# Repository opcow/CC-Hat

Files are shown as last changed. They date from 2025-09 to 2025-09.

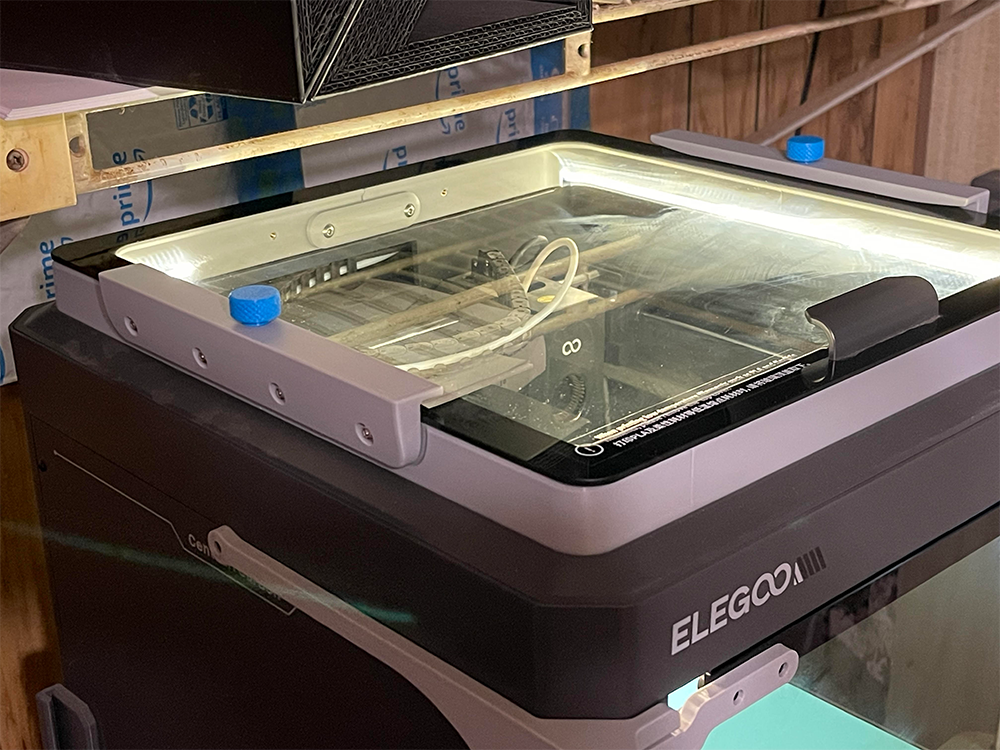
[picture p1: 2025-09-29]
images/main.png

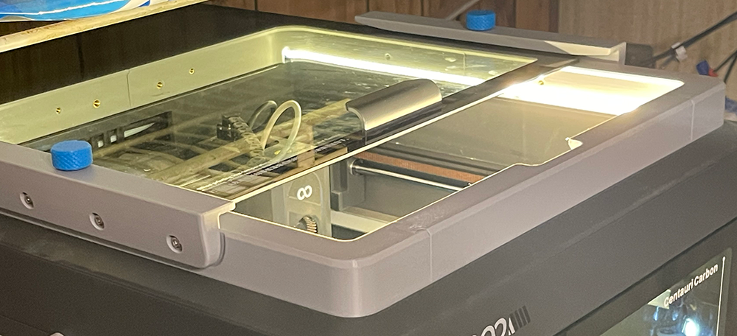
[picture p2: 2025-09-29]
images/open.png

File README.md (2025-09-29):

# CC-Hat (yet another riser)

This is my take on a lid riser for the Centauri Carbon.

I started this design using the one-piece step file for the vented riser by JesusFreak, and while there isn't very much left of the original geometry of that riser, I'm calling this a remix of JesusFreak's awesome design.

### Changes From the OG

* Reduced height to 27.5 MM.
* No vent. The riser is designed so that the lid can be slid back or forward for venting.

### Important Things to Know Before Printing

* All holes were sized for M3 and M4 threaded inserts. I have provided step files, so the holes can be resized if you prefer not to use threaded inserts (though I recommend using them for the 8 M4 screws for the glass guides).
* All holes other than the 8 glass guide holes are completely optional. Other than the guides, the parts fit together with dovetail joints which should be entirely sufficient to hold the riser together while in place on the printer.
* The dovetail joints were designed with **zero tolerance**. This makes for a perfect tight, but not too tight, fit when I print them on my printer using my slicer settings. I would strongly suggest that you print the provided test joint to ensure that these joints will work for you before printing the whole shebang. Adjust the tolerance if needed.
* The parts called plates are provided for locking the joints. These are optional. The holes are sized for M3 inserts. Resize the holes if you want to self tap screws into the plastic.
* **The thumbscrews are intended to be printed in 95A TPU**. TPU gives good friction and it would be impossible to break the glass by over-tightening the screw.
* The inside holes are meant for hooks/clamps for holding an LED strip. I use a strip with an adhesive backing and don't use these holes for anything, there are example clamp models provided.

### Other Info

The guides should allow the glass to be lifted enough for the handle screws to clear the riser frame for inserting the glass or the glass can be inserted from the rear. There is a spacer meant to go between the guide and the frame. This allows for tighter or looser horizontal tolerance between the glass and the guides. The provided spacer model is 2.1 MM thick. You will need to print 8 of these.

There is an optional glass guide without the threaded hole if you only want to use a single thumbscrew or no thumbscrews. I like using two thumbscrews, as it makes it easy to safely remove the whole riser with the glass in place (just make sure the screws are locked down first).

There is an optional rear brace provided for the inside rear dovetail joint. This part is optional, and really is overkill if you are using the rear plate part, but it's there if you want.

### Print Materials and Settings

Use whatever you want for the frame and guides. PLA or PETG should be fine.

As stated above, I recommend 95A TPU for the thumbscrews. I haven't tried other materials. The purpose of the screws is to hold the glass in place when closed or when open for venting. You could adjust the spacers to achieve enough friction between the glass and the guides to keep the glass in place. I have not tested this.

The front part of the frame must be printed at 45 degrees on a 256 x 256 build plate. I change the sparse infill direction to 0 and the solid infill to 90 to compensate.

I used Orca Slicer's 0.20 MM Strength preset with gyroid for the frame, which I printed in Voxel PLA.

I used the 0.16 MM Optimal preset with gyroid infill for the guides, which were also printed in Voxel PLA.

I used the 0.16 MM Optimal preset with gyroid infill for the thumbscrews, which were printed in Polymaker 95A TPU.

I use scarf joint seam, nearest for my seam settings and I can't even tell where the seams are, but use whatever you prefer.

### Required Extras

* 8 M4 x 12 MM button head screws. Socket cap may be okay, as well, but you might want to use a washer.
* 8 M4 threaded inserts (or resize the holes for self-tapping).
* Optionally, 7 M3 x 8 MM counter-sink socket head screws and M3 inserts (or resize the holes for self-tapping).
* 2 M4 screws and inserts if you want the rear joint brace, but this part isn't really recommended if you are using the three plates that go under the joints.

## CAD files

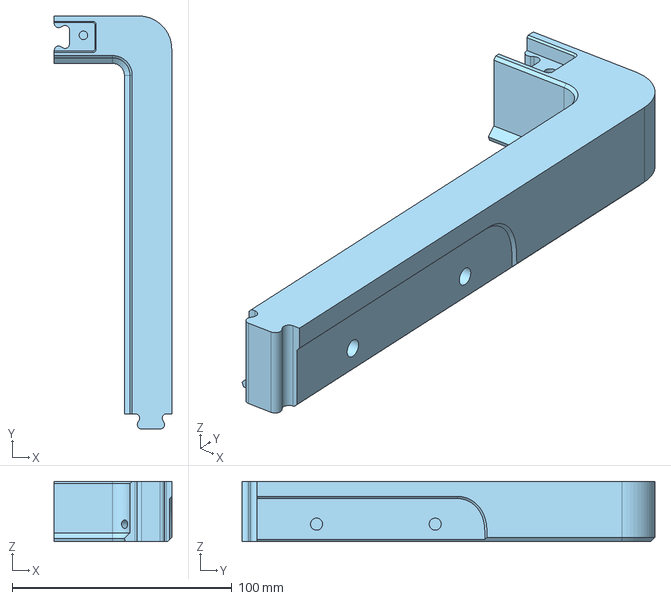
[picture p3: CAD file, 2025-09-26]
STEP/front-right.step
53.5 x 187.9 x 27.5 mm

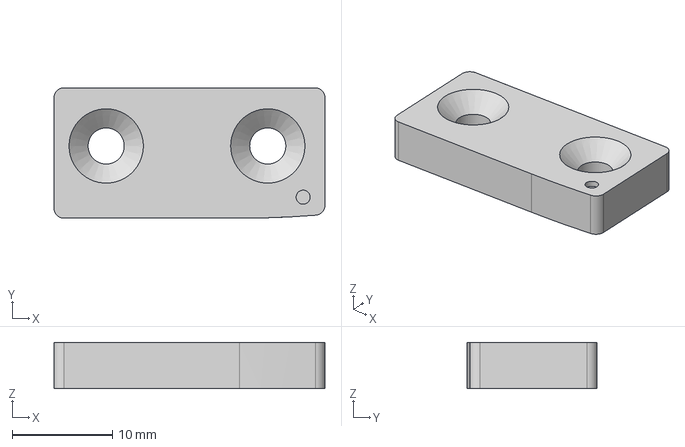
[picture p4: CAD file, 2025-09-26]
STEP/plate-left.step
27.0 x 13.0 x 4.60 mm

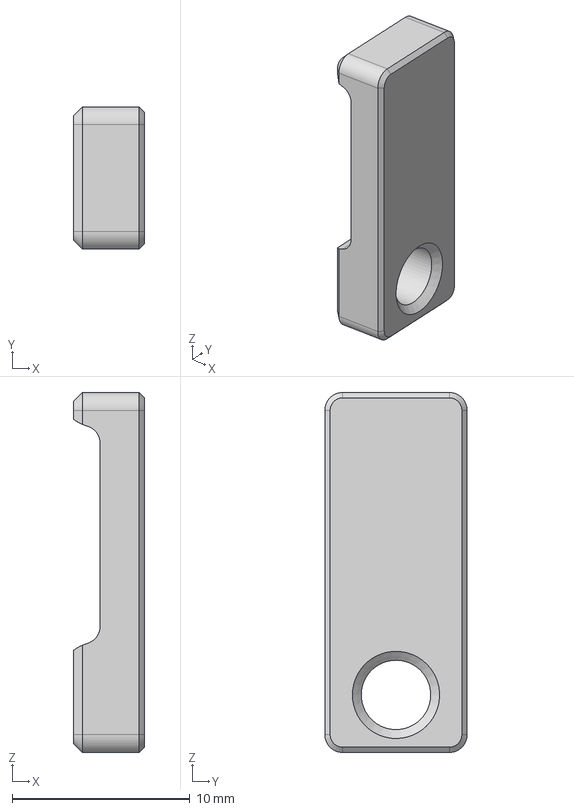
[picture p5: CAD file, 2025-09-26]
STEP/clamp.step
4.00 x 8.00 x 20.2 mm

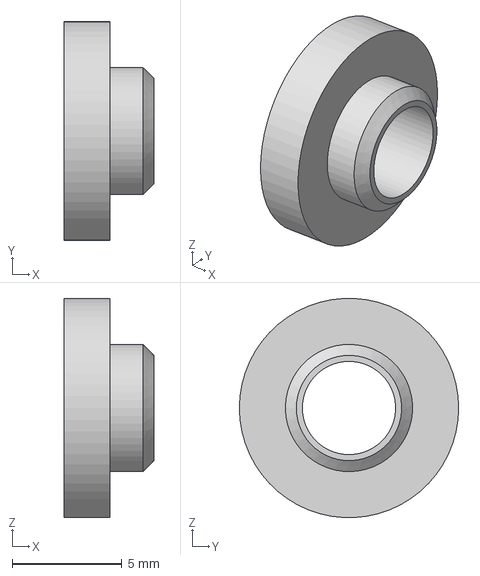
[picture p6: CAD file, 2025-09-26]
STEP/spacer.step
4.10 x 10.0 x 9.99 mm

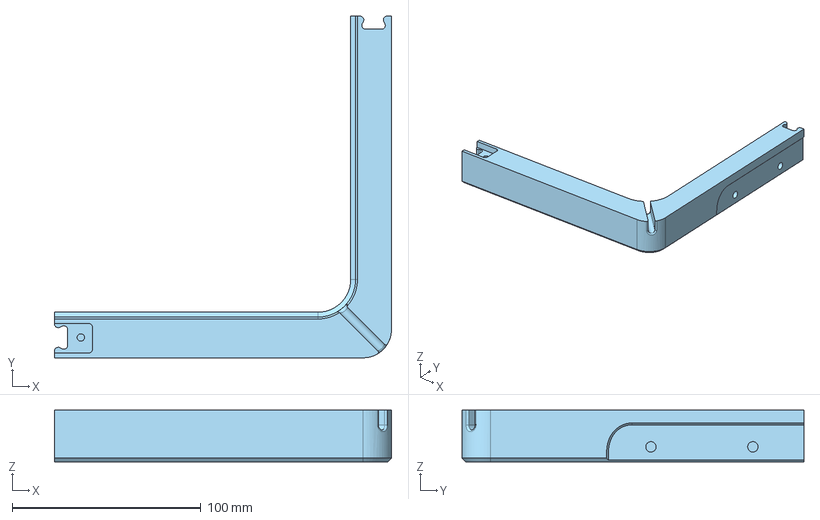
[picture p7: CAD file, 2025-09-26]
STEP/back-right.step
178.5 x 181.0 x 27.5 mm

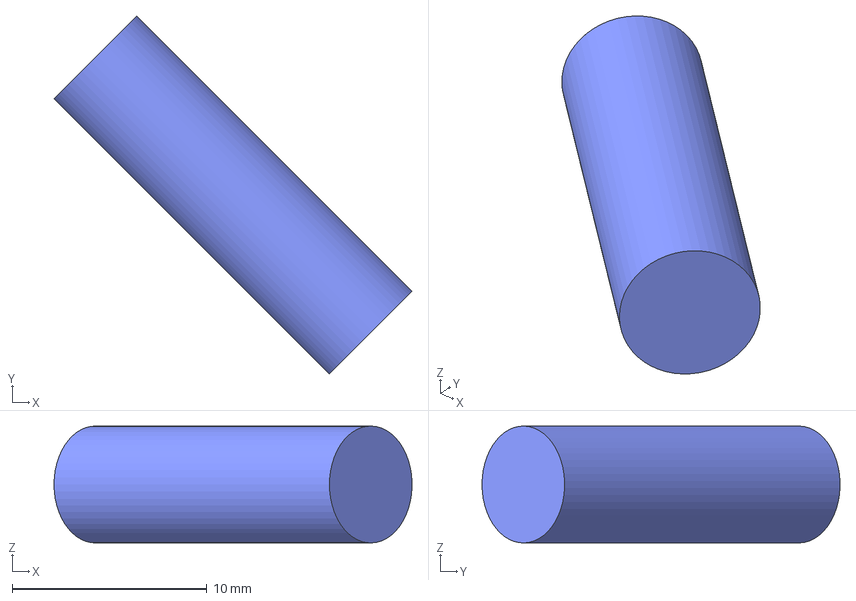
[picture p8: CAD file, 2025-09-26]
STEP/plug.step
18.4 x 18.4 x 6.00 mm

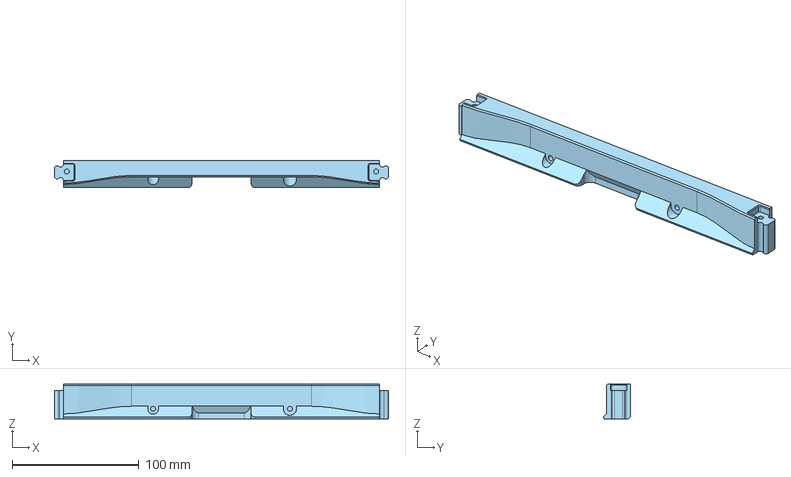
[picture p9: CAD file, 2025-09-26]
STEP/front.step
263.9 x 21.6 x 27.5 mm

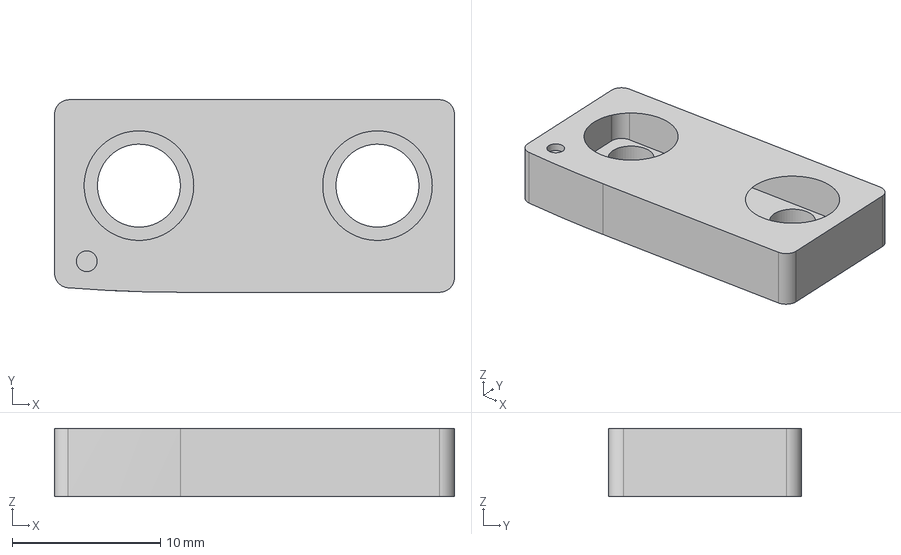
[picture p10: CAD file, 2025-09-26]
STEP/plate-right.step
27.0 x 13.0 x 4.60 mm

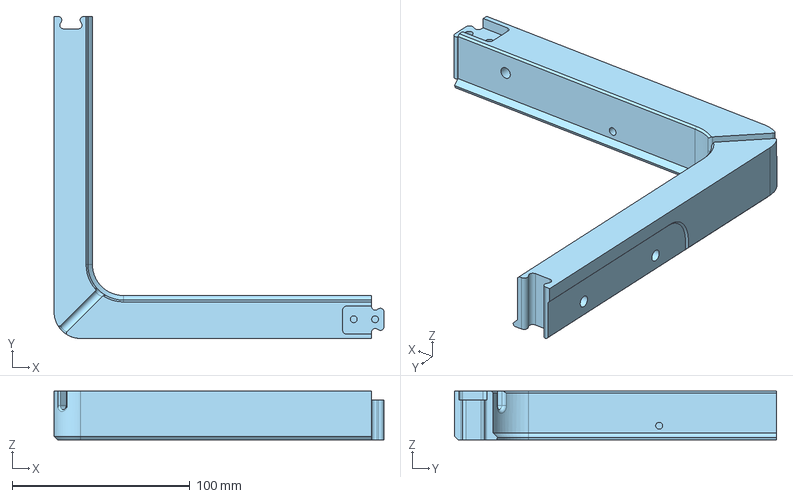
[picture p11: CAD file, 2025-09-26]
STEP/back-left.step
185.4 x 181.0 x 27.5 mm

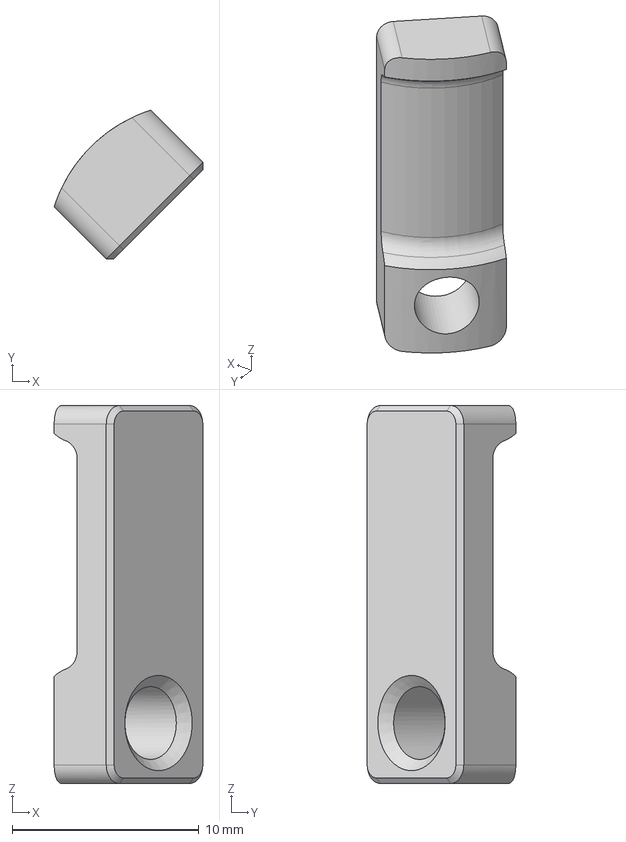
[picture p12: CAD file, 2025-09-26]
STEP/corner-clamp.step
7.96 x 7.96 x 20.2 mm

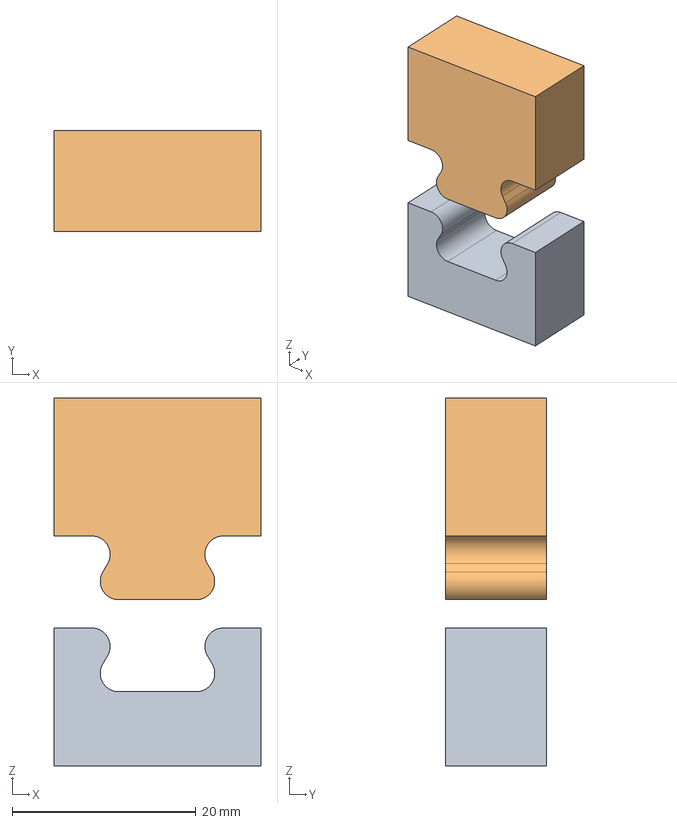
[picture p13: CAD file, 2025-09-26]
STEP/test-joint.step
22.5 x 11.0 x 40.0 mm

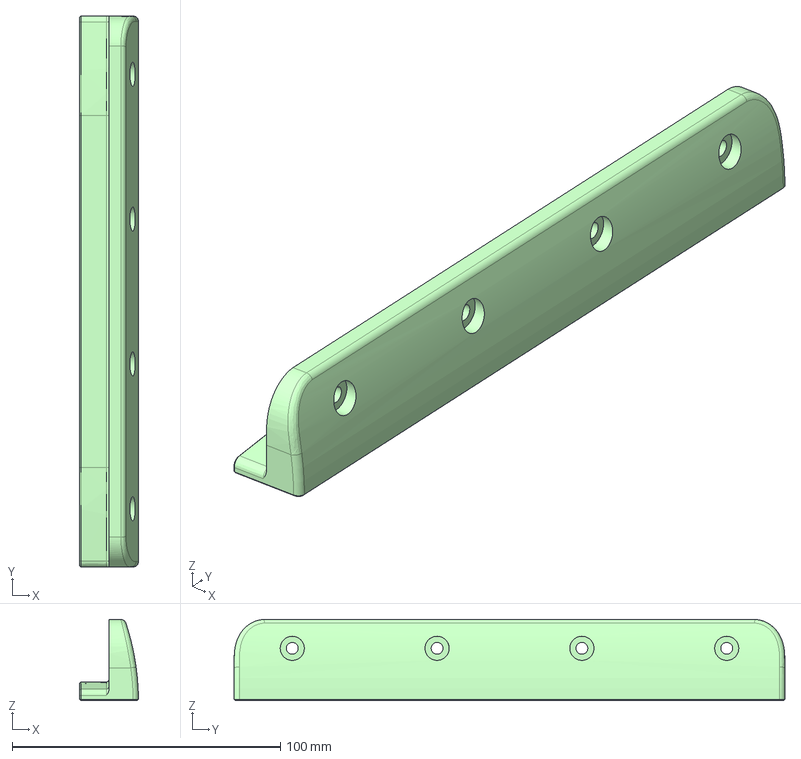
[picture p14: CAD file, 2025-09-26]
STEP/guide.step
22.0 x 205.5 x 30.3 mm

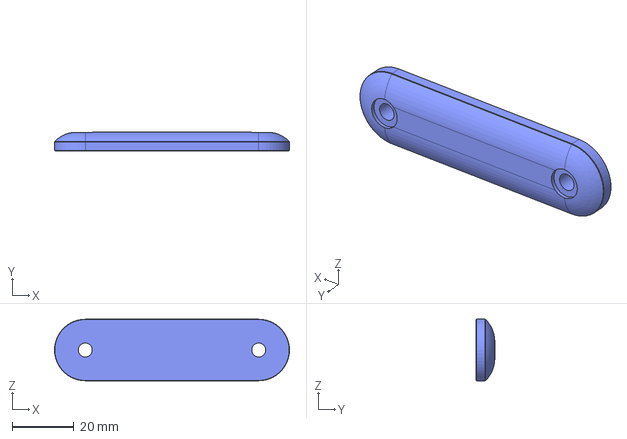
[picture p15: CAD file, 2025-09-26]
STEP/rear-brace.step
76.0 x 6.00 x 19.9 mm

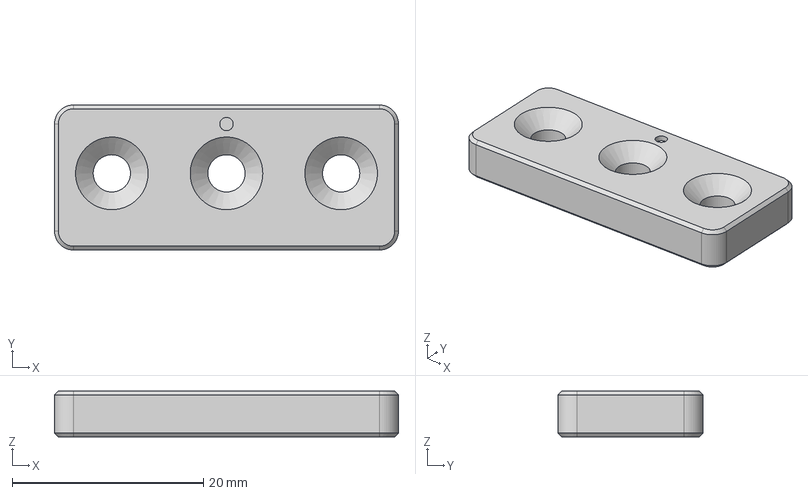
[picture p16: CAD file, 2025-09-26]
STEP/plate-rear.step
36.0 x 15.2 x 4.80 mm

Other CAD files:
STEP/front-left.step
STEP/screw.step
STEP/guide-no-screw.step
STL/back-left.stl
STL/back-right.stl
STL/clamp.stl
STL/corner-clamp.stl
STL/front-left.stl
STL/front-right.stl
STL/front.stl
STL/guide-no-screw.stl
STL/guide.stl
STL/plate-left.stl
STL/plate-rear.stl
STL/plate-right.stl
STL/plug.stl
STL/rear-brace.stl
STL/screw.stl
STL/spacer.stl
STL/test-joint.stl
